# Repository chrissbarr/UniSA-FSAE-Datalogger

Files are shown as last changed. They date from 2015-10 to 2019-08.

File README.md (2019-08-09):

# UniSA FSAE Datalogger
This is an Arduino shield designed to be used for logging data on the UniSA SAE Team's vehicle. It provides interfaces to various components - primarily sensors, but there are also user-interface elements as well.

## Image
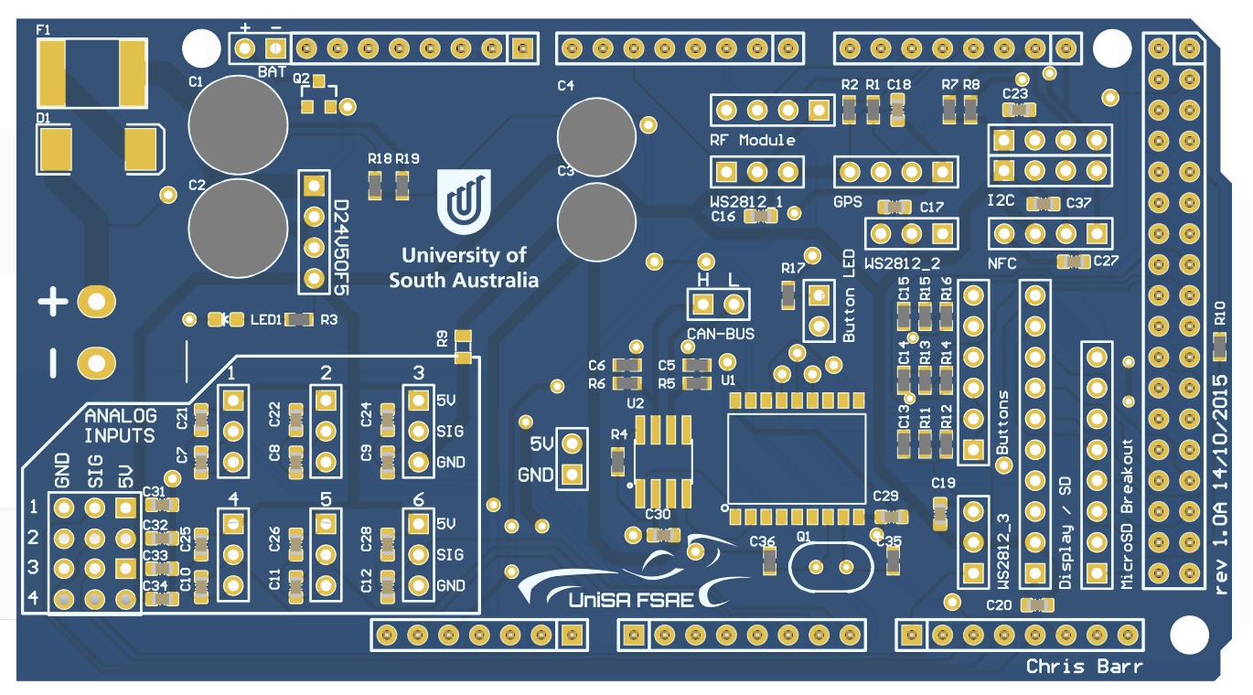
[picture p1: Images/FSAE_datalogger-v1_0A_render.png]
FSAE Datalogger PCB Preview


## Connections
### Sensor Inputs
* GPS
* IR Thermopile
* Thermistors
* Potentiometers
* CAN Bus

### User Interface
* Adafruit OLED Display
* Physical Push-buttons
* NFC Tag Read / Write

### Outputs
* Log Data to microSD Card
* Transmit Data via Wireless Link (UART-based)
* Power and Control WS2812 LEDs for Indication and Illumination

### Power
* Board space / pin header to connect a [Pololu D24V50F5](https://www.pololu.com/product/2851) step-down voltage regulator.
 * 7-38V Input
 * Max. 5A Current
* SMD fuse for short-circuit protection
* Diode for reverse-polarity protection

## Compatibility
Originally designed to be compatible with the Arduino Due, problems with I2C communication between some of the peripherals (primarily the NFC module) and the Due caused a shift to the Arduino Mega2560. Form factor remains unchanged, and the Due may still be useable provided the compatibility issue is overcome or disregarded.

The primary concern is sufficient IO, which the Arduino Uno (and other similar form-factor boards) were lacking. Use of the Arduino Due would allow for the CAN Bus controller inside the AT91SAM3X8E to be used (removing the need for the MCP2515 CAN Bus controller IC).

## Design Images
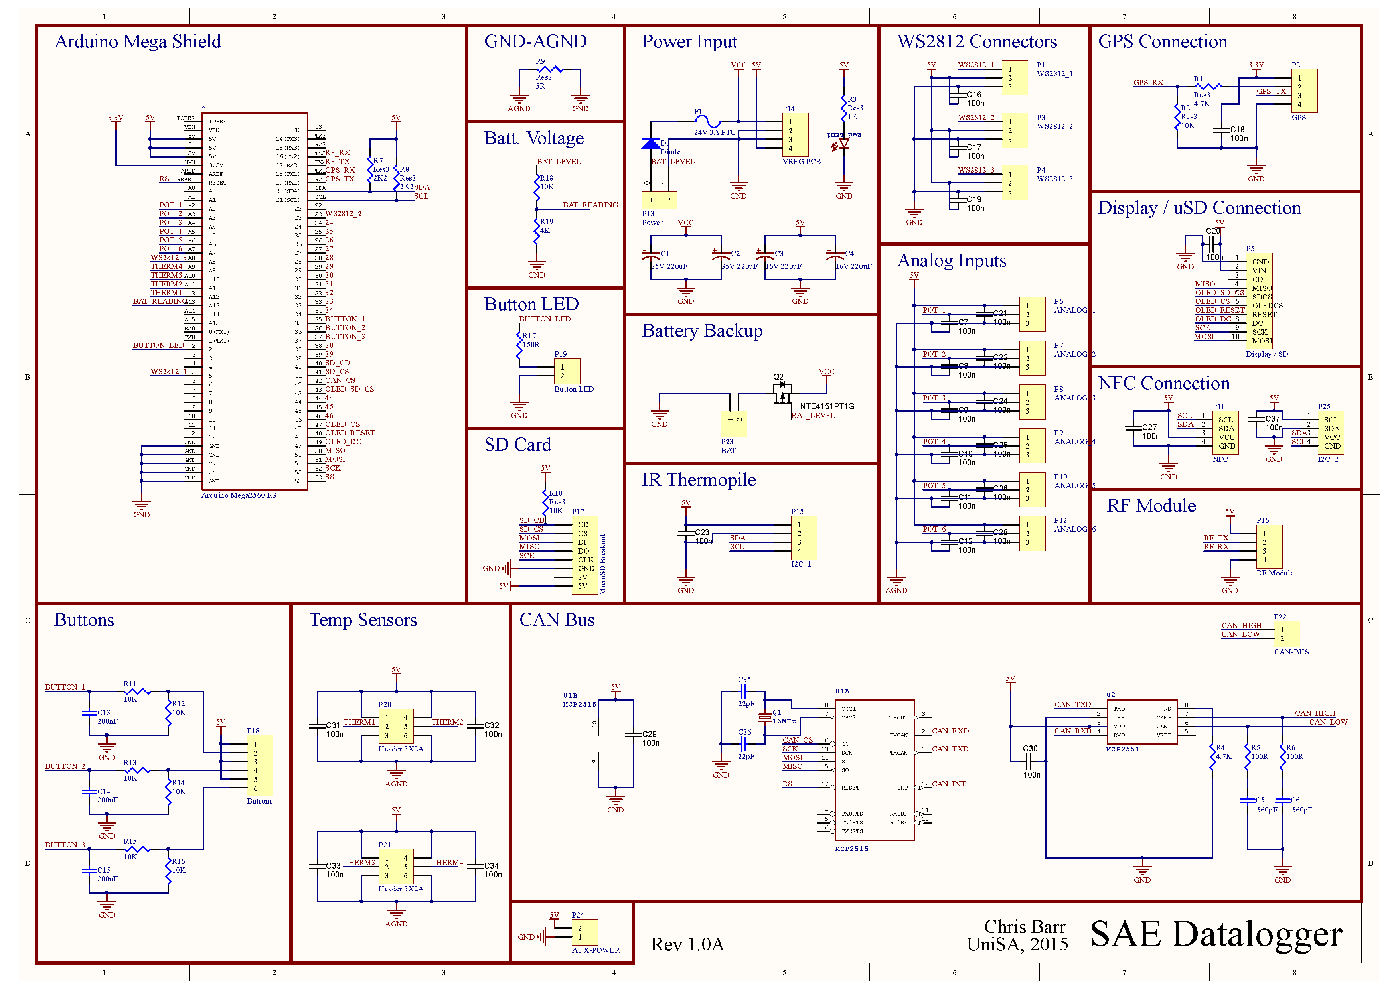
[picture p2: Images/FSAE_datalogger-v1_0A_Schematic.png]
FSAE Datalogger Schematic


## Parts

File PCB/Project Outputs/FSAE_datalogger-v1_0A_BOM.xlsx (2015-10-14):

Designator | Manufacturer | Manufacturer Part Number | Digikey | Comment | Description | Footprint | LibRef | Quantity
C1, C2 | Panasonic Electronic Components | ECA-1VM221 | P5166-ND | 35V 220uF | Electrolytic Capacitor | 8-DIA-CAP-3.5MM-LEADS | Capacitor 50V 470uF | 2
C35, C36 | TDK Corporation | C1608C0G1H220J080AA | 445-1273-1-ND | 22pF | Ceramic Capacitor | 0603 | Cap Semi | 2
C5, C6 | TDK Corporation | C1608C0G1H561J080AA | 445-1290-1-ND | 560pF | Ceramic Capacitor | 0603 | Cap | 2
C13, C14, C15 | TDK Corporation | C1608X7R1C224K080AC | 445-1318-1-ND | 220nF | Ceramic Capacitor | 0603 | Cap | 3
C3, C4 | Panasonic Electronic Components | ECA-1CHG221 | P5530-ND | 16V 220uF | Electrolytic Capacitor | 6.3-DIA-CAP | Capacitor 50V 470uF | 2
C7, C8, C9, C10, C11, C12, C16, C17, C18, C19, C20, C21, C22, C23, C24, C25, C26, C27, C28, C29, C30, C31, C32, C33, C34 | TDK Corporation | C1608X7R1H104K080AA | 445-1314-1-ND | 100nF | Ceramic Capacitor | CAPC1608X90N | CAPC_100n_0603_X7R_50V_10% | 25
D1 | Diodes Incorporated | S5BC-13-F | S5BC-FDICT-ND | Diode | Default Diode | SMC | Diode | 1
F1 | Bourns Inc. | MF-LSMF300/24X-2CT-ND | MF-LSMF300/24X-2CT-ND | 24V 3A PTC | Fuse | MF-LSMF SMD PTC Fuse | Fuse 2 | 1
LED1 | Kingbright | APT1608SURCK | 754-1123-1-ND | Red | Power Indicator | LED-0603 | LED0603 | 1
P1, P3, P4, P6, P7, P8, P9, P10, P12 |  |  |  | WS2812_1 | Header, 3-Pin | HDR1X3 | Header 3 | 9
P2, P11, P14, P15, P16 |  |  |  | GPS | Header, 4-Pin | HDR1X4 | Header 4 | 5
P5 |  |  |  | Display / SD | Header, 10-Pin | HDR1X10 | Header 10 | 1
P13 | On Shore Technology Inc. | OSTTC022162 | ED2609-ND | Power | Screw Terminal, 2-Pin | 2P 5.08mm Screw Terminal | 2P Screw Terminal 5.08mm | 1
P17 |  |  |  | MicroSD Breakout | Header, 8-Pin | HDR1X8 | Header 8 | 1
P18 |  |  |  | Buttons | Header, 6-Pin | HDR1X6 | Header 6 | 1
P19, P22, P23, P24 |  |  |  | Button LED | Header, 2-Pin | HDR1X2 | Header 2 | 4
P20, P21 |  |  |  | Header 3X2A | Header, 3-Pin, Dual row | HDR2X3_CEN | Header 3X2A | 2
Q1 | ECS Inc. | ECS-160-20-46X | XC1759-ND | 16MHz | CrystalsVarious standard crystals. Proven footprints. Spark Fun Electronics SKU : COM-00534 | CRYSTAL-SMD-5X3 | CRYSTAL5X3 | 1
Q2 | ON Semiconductor | NTE4151PT1G | NTE4151PT1GOSCT-ND | P-Channel | MOSFET SMD P-CH 20V 0.76A 0.313W SOT523F | SOT23-3 | MOSFET_P-CH_NTE4151PT1G | 1
R1, R4 | Yageo | RC0603JR-074K7L | 311-4.7KGRCT-ND | 4.7K | Resistor | 0603 | Res3 | 2
R7, R8 | Yageo | RC0603FR-072K2L | 311-2.20KHRCT-ND | 2K2 | Resistor | 0603 | Res3 | 6
R3 | Yageo | RC0603JR-071KL | 311-1.0KGRCT-ND | 1K | Resistor | 0603 | Res3 | 1
R5, R6 | Yageo | RC0603JR-07100RL | 311-100GRCT-ND | 100R | Resistor | 0603 | Res3 | 2
R9 | Yageo | RC0603JR-071RL | 311-1.0GRCT-ND | 1R | Resistor | 0805 | Res3 | 1
R2, R10, R11, R12, R13, R14, R15, R16, R18 | Yageo | RC0603JR-0710KL | 311-10KGRCT-ND | 10K | Resistor | 0603 | Res3 | 6
R17 | Yageo | RC0603JR-07150RL | 311-150GRCT-ND | 150R | Resistor | 0603 | Res3 | 1
R19 | Yageo | RC0603FR-074K02L | 311-4.02KHRCT-ND | 4K | Resistor | 0603 | Res3 | 2
U1 | Microchip Technology | MCP2515T-I/SO | MCP2515T-I/SOCT-ND | MCP2515 | CAN Controller | SO-18W | MCP2510SO | 1
U2 | Microchip Technology | MCP2551-I/SN | MCP2551-I/SN-ND | MCP2551 | CAN Transciever | SO08 | MCP2551 | 1

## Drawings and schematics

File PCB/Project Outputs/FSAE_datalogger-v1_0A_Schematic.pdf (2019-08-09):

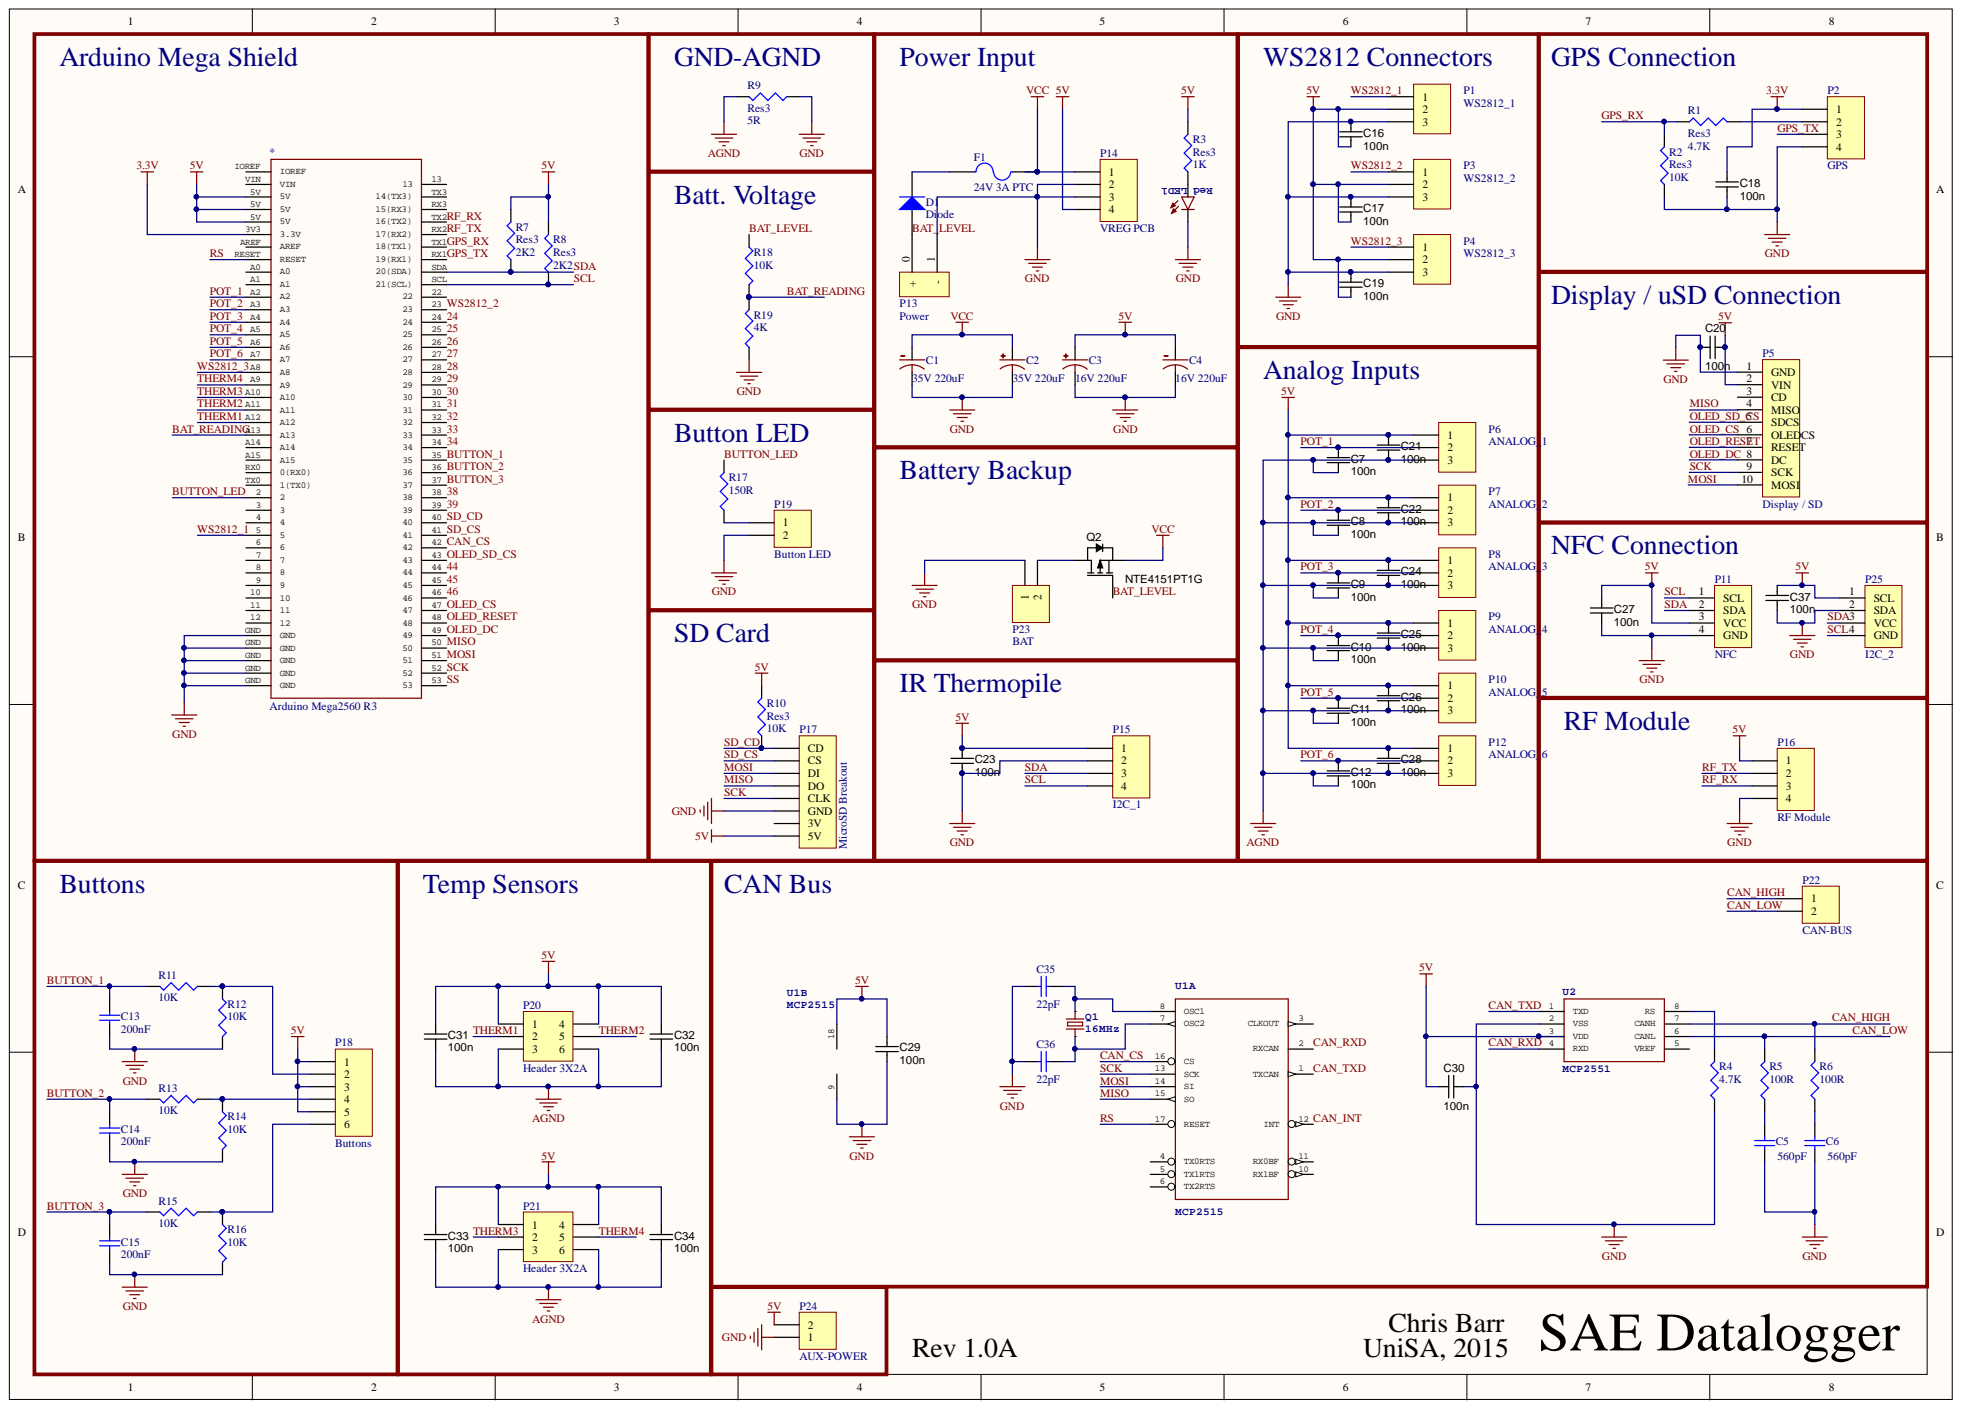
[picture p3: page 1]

5V 5V

GND

SAE Datalogger Chris Barr

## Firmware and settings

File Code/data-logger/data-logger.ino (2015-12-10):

/**************************************************************************/
/*! 
    Datalogger sketch for the UniSA FSAE team.
    
*/
/**************************************************************************/

#define _CAT(a, ...) a ## __VA_ARGS__
#define SWITCH_ENABLED_0 0
#define SWITCH_ENABLED_1 1
#define SWITCH_ENABLED_  1
#define ENABLED(b) _CAT(SWITCH_ENABLED_, b)

#define NFC
#define GPS
#define DISPLAY
#define SDCARD 1  //1 for SD card in display, 2 for SD card in separate breakout
#define BUTTONS
#define EEPROM_ENABLED
#define ANALOG_INPUTS
#define CANBUS


#include <stdio.h>

//NFC Setup
#if ENABLED(NFC)
  //#include <Wire.h>
  #include <PN532_I2C.h>
  #include <PN532.h>
  //#include <NfcAdapter.h>

  PN532_I2C pn532i2c(Wire);
  PN532 nfc(pn532i2c);
#endif

//GPS SETUP
#if ENABLED(GPS)
  #include <TinyGPS++.h>
  
  static const uint32_t GPSBaud = 9600;
  TinyGPSPlus gps;  // The TinyGPS++ object
  
#endif

//Display SETUP
#if ENABLED(DISPLAY)
  #include <Adafruit_GFX.h>
  #include <Adafruit_SSD1351.h>
  #include <SD.h>
  #include <SPI.h>
  
  //#define VERBOSE_DISPLAY
  #define SPLASH_SCREEN_ENABLED
  #define SPLASH_IMAGE "splash.bmp" //file to load from SD card. 
  #define SPLASH_DURATION 1000 //display duration in milliseconds
  
  //OLED Setup
  // You can use any (4 or) 5 pins 
  #define sclk 2
  #define mosi 3
  #define dc   49
  #define cs   47
  #define rst  48
  
  // Color definitions
  #define	BLACK           0x0000
  #define	BLUE            0x001F
  #define	RED             0xF800
  #define	GREEN           0x07E0
  #define CYAN            0x07FF
  #define MAGENTA         0xF81F
  #define YELLOW          0xFFE0  
  #define WHITE           0xFFFF
    
  // use the hardware SPI pins 
  Adafruit_SSD1351 tft = Adafruit_SSD1351(cs, dc, rst);
  
  String output;
  char char_buff[20];

#endif

//SD SETUP
#if ENABLED(SDCARD)
    #define SD_CS 43    

    // the file itself
    File bmpFile;
    
    // information we extract about the bitmap file
    int bmpWidth, bmpHeight;
    uint8_t bmpDepth, bmpImageoffset;

    const int LIMIT = 1000;
    char fileName[13];
    File dataFile;
#endif

//Button SETUP
#if ENABLED(BUTTONS)
  #include <Button.h>        //https://github.com/JChristensen/Button
  #define BUTTON_UP 36
  #define BUTTON_SEL 35
  #define BUTTON_SET 37

  #define PULLUP false
  #define INVERT false
  #define DEBOUNCE_MS 20
  #define LONG_PRESS 1000

  Button button_up(BUTTON_UP, PULLUP, INVERT, DEBOUNCE_MS);    //Declare the button
  Button button_sel(BUTTON_SEL, PULLUP, INVERT, DEBOUNCE_MS);    //Declare the button
  Button button_set(BUTTON_SET, PULLUP, INVERT, DEBOUNCE_MS);    //Declare the button

#endif

#if ENABLED(EEPROM_ENABLED)
  #include <EEPROM.h>

  int eeprom_address = 0;
  int eeprom_options_start_addr = 0;
#endif

#if ENABLED(ANALOG_INPUTS) 
  #define ANALOG1 A2
  #define ANALOG2 A3
  #define ANALOG3 A4
  #define ANALOG4 A5
  #define ANALOG5 A6
  #define ANALOG6 A7

  #define SAMPLE_FREQ 4 //every x'th loop sample and store values

  int analog1, analog2, analog3, analog4, analog5, analog6;
#endif

#if ENABLED(CANBUS) 
  #include <Canbus.h>

  int data;
  char buffer[456];  //Data will be temporarily stored to this buffer before being written to the file
#endif

//timekeeping
#define LOOP_DELAY 20000 // Loop delay in us. This is the desired time between drive calls. Stability ensures accurate velocity calculations and motor control.

// Can put variables for checking accurate loop timing here, eg interupt time and scale factor.
int loop_number = 0; // variable to hold the loop number. Used to keep track of which topics to publish and when
unsigned long loop_time = micros(); // Loop time place holder for motor velocity calculation.
unsigned long last_loop_micros = micros();

int loop_index = 0;

//menu structure
#define MENU_OPTIONS 6
#define MENU_OPTION_HEIGHT 10
int menu_selected_index = 0;
bool menu_changed = false;
bool menu_changed_small = false;
bool menu_active = false;
bool menu_just_opened = false;

enum menu_items {
  GPS_ONOFF,
  LED_BRIGHTNESS,
  SD_LOGGING,
  INVERT_DISPLAY,
  CLEAR_EEPROM,
  NEW_LOGFILE
};

typedef struct menuOption {
  String optionName;
  int numStates;
  int curState;
  String stateText[5];
};

struct menuOption menuArray[MENU_OPTIONS];


//variables to format and display to driver

enum display_variables {
  V_SPEED,
  V_SPEED_AVG,
  V_RPM,
  V_VOLTS,
  V_TEMP,
  V_AMPS,
  V_POWER
};

enum variable_types {
  INT,
  FLOAT,
  BOOL,
  STRING
};

#define NUM_VARIABLES 4

typedef struct displayVariable {
  int type;
  int intVal;
  float floatVal;
  bool boolVal;
  String stringVal;
  String displaySymbol;
  String displayPrefix;
  String displaySuffix;
  int decPoints;
  bool valChanged;
  int symOffset;
};

struct displayVariable displayVariables[NUM_VARIABLES];

long randNumber;
int activeVariableBig = 0;
int activeVariableSmall1 = 0;
int activeVariableSmall2 = 0;
bool indicatorsJustChanged = false;

#define BATT_PIN A13
#define BATT_R1 10000
#define BATT_R2 4000

void setup(void) {
  Serial.begin(115200);

  menu_init();
  variables_init();

  pinMode(cs, OUTPUT);
  digitalWrite(cs, HIGH);  

  #if ENABLED(DISPLAY)
    display_init();
  #endif

  #if ENABLED(SDCARD)
    Serial.print("Initializing SD card...");
  
    if (!SD.begin(SD_CS)) {
      Serial.println("failed!");
      return;
    }
    Serial.println("SD OK!");
  
    #if ENABLED(SPLASH_SCREEN_ENABLED)
      bmpDraw(SPLASH_IMAGE, 0, 0);
      delay(SPLASH_DURATION);
      tft.fillScreen(BLACK);
    #endif

    sd_new_logfile();
  
  #endif

  #if ENABLED(DISPLAY)

    if(nfc_init() && gps_init() && eeprom_init()) {
      tft.setTextColor(GREEN);
      tft.println("All systems pass");   
    } else {
      tft.setTextColor(RED);
      tft.setTextSize(3);
      tft.println("Error");   
      tft.setTextSize(1);
      while(1 < 2);
    }
    tft.setTextColor(WHITE); 

    delay(500);

    tft.fillScreen(BLACK);  
    
  #endif

  randomSeed(analogRead(0));
}

void loop(void) {

  loop_timing(); 

  if(loop_index == 0) {
    calculate_voltage();
    loop_index++;
  } else if (loop_index == 1) {
    gps_update();
    loop_index++;
  } else if (loop_index == 2) {
    analog_update();
    loop_index++;
  } else if (loop_index == 3) {
    log_to_sd();
  } else if (loop_index == 4) {
    displayVariables[V_RPM].intVal = canbus_get_rpm();
    loop_index = 0;
  }

  button_update();

  // operate menu / status display
  menu_buttons();   
  if(menu_active) {
    menu_draw();
  } else {
    status_draw();
  }
    
  //nfc_update();
  update_actions();

  // test changing variable (speed)
  randNumber = random(10);

  if(randNumber == 2) {
    displayVariables[V_SPEED].floatVal += (random(-500,500)/1000.0);
    displayVariables[V_SPEED].valChanged = true;
  }

}

void status_draw() {
  
  bool blankScreen = false; //if true, screen will be erased (i.e. when switching from menu to status)
  
  if (button_up.pressedFor(LONG_PRESS) && indicatorsJustChanged == false) {
    Serial.println("Changing big variable...");
    activeVariableBig++;
    indicatorsJustChanged = true;
    blankScreen = true;
  
    if (activeVariableBig >= NUM_VARIABLES)
      activeVariableBig = 0;
  }

  if(menu_changed) {
    blankScreen = true;
    menu_changed = false;
    indicatorsJustChanged = true;
  }

  if(blankScreen) {
    tft.fillScreen(BLACK);  
    print_variable_big(activeVariableBig, 20, 20, 2, WHITE);
  } 
  
  if(indicatorsJustChanged) {
    displayVariables[activeVariableBig].valChanged = true;
  } 
    
  print_variable_big(activeVariableBig, 20, 20, 2, WHITE);

  if(indicatorsJustChanged && button_up.wasReleased())
    indicatorsJustChanged = false; 
}

////////////////////////////////////////////////////////////////////
//                        GENERAL FUNCTIONS                       //
////////////////////////////////////////////////////////////////////

//checks and tracks state of buttons, call frequently
void button_update() {
  button_up.read();
  button_sel.read();
  button_set.read();
}

//maintains consistent loop timing, assuming LOOP_DELAY is large enough
void loop_timing()
{
  while(micros() - last_loop_micros < LOOP_DELAY - 10)
  {
    delayMicroseconds(20); // This loop timing is inaccurate and does not take processing time into account. A better timing function is required.
  }
  //unsigned long temp_last_micros = last_loop_micros;
  last_loop_micros = micros();
  //Serial.println(last_loop_micros-temp_last_micros);
}

//Used to print "GPS...     " etc consistently when initialising
//called by initialisation functions upon startup
void beginTestPrint(char *moduleName) {
  tft.print(moduleName);
  tft.print("...");
  for(int i = 0; i < 14-strlen(moduleName); i++)
    tft.print(" ");
}

//Used to print "pass" or "fail" etc consistently when initialising
//called by initialisation functions after success / failure
void completeTestPrint(bool pass) {
  if(!pass) {
    tft.setTextColor(RED);
    tft.print("FAIL");
  } else {
    tft.setTextColor(GREEN);
    tft.print("pass");
  }
  tft.setTextColor(WHITE);
}

////////////////////////////////////////////////////////////////////
//                             CAN-BUS                            //
////////////////////////////////////////////////////////////////////

bool canbus_init() {
  #if ENABLED(CANBUS) 
    bool success;
    beginTestPrint("CAN-BUS");
    if(Canbus.init(CANSPEED_500))  /* Initialise MCP2515 CAN controller at the specified speed */
      {
        Serial.println("CAN Init ok");
        success = true;
      } else
      {
        Serial.println("Can't init CAN");
        success = false;
      } 
  
      completeTestPrint(success);
      return success;
    #else
      return true;
    #endif
}

int canbus_get_rpm() {
  
  int engine_rpm = 5000;
  
  #if ENABLED(CANBUS) 
    Canbus.ecu_req(ENGINE_RPM, buffer);
    Serial.print("Engine RPM: ");
    Serial.println(buffer);

    engine_rpm = atoi(buffer);
  #endif

  return engine_rpm;    
}

////////////////////////////////////////////////////////////////////
//                           OLED DISPLAY                         //
////////////////////////////////////////////////////////////////////

bool display_init() {
  tft.begin();
  //tft.setRotation(1);
  tft.fillScreen(BLACK);
  //tft.setTextColor(WHITE);
  //tft.print("Display...    ");
  //tft.setTextColor(GREEN);
  //tft.println("pass"); 
  tft.setTextColor(WHITE);
  return true;
}

void displayTest() {
  for(int i = 0; i < 100; i++) {
    displayPrint("Test ",WHITE);
    tft.println(i);
    
    delay(500);
  }
}

//deprecated I think, just use tft.print(etc) - much more flexible and built in.
void displayPrint(char *text, uint16_t color) {
  if(tft.getCursorY()>tft.height()-10) {
    tft.fillScreen(BLACK);
    tft.setCursor(0,0);
  }
  tft.setTextColor(color);
  tft.print(text);
  Serial.print(text);
}

////////////////////////////////////////////////////////////////////
//                   VARIABLE DISPLAY FORMATTING                  //
////////////////////////////////////////////////////////////////////

//configure different variables for display. These variables are also logged automatically.
//To add new variables, add variable ENUM to the ENUM list before setup. Increase variable count define.
//Add variable details below.
void variables_init() {
  displayVariables[V_SPEED].type = FLOAT;
  displayVariables[V_SPEED].floatVal = 75;
  displayVariables[V_SPEED].displaySuffix = "km/h";
  displayVariables[V_SPEED].displaySymbol = "VEL";
  displayVariables[V_SPEED].decPoints = 1;
  displayVariables[V_SPEED].valChanged = true;
  displayVariables[V_SPEED].symOffset = 0;

  displayVariables[V_SPEED_AVG].type = FLOAT;
  displayVariables[V_SPEED_AVG].floatVal = 5;
  displayVariables[V_SPEED_AVG].displaySuffix = "km/h";
  displayVariables[V_SPEED_AVG].displaySymbol = "AVG";
  displayVariables[V_SPEED_AVG].decPoints = 1;
  displayVariables[V_SPEED_AVG].valChanged = true;
  displayVariables[V_SPEED_AVG].symOffset = 20;

  displayVariables[V_RPM].type = INT;
  displayVariables[V_RPM].intVal = 2500;
  displayVariables[V_RPM].displaySymbol = "RPM";
  displayVariables[V_RPM].valChanged = true;
  displayVariables[V_RPM].symOffset = 40;

  displayVariables[V_VOLTS].type = INT;
  displayVariables[V_VOLTS].intVal = 0;
  displayVariables[V_VOLTS].displaySymbol = "BAT";
  displayVariables[V_VOLTS].displaySuffix = "V";
  displayVariables[V_VOLTS].valChanged = true;
  displayVariables[V_VOLTS].symOffset = 60;
}

//prints a given variable at a chosen size, selectable coordinates, colour etc.
// draws the 'symbol' ('VEL', 'REV', 'TEMP' etc above value at location set on variable creation.
// only draws on variable change - to force, set displayVariables[var].valChanged = true;
void print_variable_big(int var, int x, int y, int t_size, uint16_t color) {

  if(displayVariables[var].valChanged == true) {
    
    String variableValue = formatted_variable(var);
  
    int symOffsetX = 0+displayVariables[var].symOffset;
    int symOffsetY = -10;
    int width = (variableValue.length() * (5 * t_size)) - symOffsetX;
    int height = (7 * t_size) - symOffsetY;
  
    tft.fillRect(x+symOffsetX,y+symOffsetY,width,height,BLACK);
  
    tft.setCursor(x,y);
    tft.setTextColor(color);
    tft.setTextSize(t_size);
  
    tft.print(variableValue);
    
    tft.setTextSize(1);
    tft.setCursor(x+symOffsetX,y+symOffsetY);
    
    tft.print(displayVariables[var].displaySymbol);

    displayVariables[var].valChanged = false;
  }
}

//returns a formatted string containing a given variable, 
//including any prefix and suffix (i.e. 'km/h', 'W', 'A', 'V', '/s')
String formatted_variable(int var) {
  String formatted;
  
  formatted = displayVariables[var].displayPrefix;
  
  formatted += string_variable(var);

  formatted += displayVariables[var].displaySuffix;

  return formatted;
}

//I'm retarded, there's a better way to do this I'm sure. Mental block, I swear.
//Variables can be int, float, boolean or string - we want one interface regardless.
//function takes in variable index and returns string containing variable, with no 
//knowledge of variable type required as input.
//These strings are used to build the text displayed to the user, and this value 
//is also directly used when logging to the SD card.
String string_variable(int var) {
  if(displayVariables[var].type == INT)
    return String(displayVariables[var].intVal);
  if(displayVariables[var].type == FLOAT)
    return String(displayVariables[var].floatVal,displayVariables[var].decPoints);
  if(displayVariables[var].type == BOOL)
    return String(displayVariables[var].boolVal);
  else
    return displayVariables[var].stringVal;
}


////////////////////////////////////////////////////////////////////
//                         MISC INPUTS                            //
////////////////////////////////////////////////////////////////////

//reads the analog inputs designed for potentiometers (or similar), spaced separately on the board.
void analog_update() {
  analog1 = analogRead(ANALOG1);
  analog2 = analogRead(ANALOG2);
  analog3 = analogRead(ANALOG3);
  analog4 = analogRead(ANALOG4);
  analog5 = analogRead(ANALOG5);
  analog6 = analogRead(ANALOG6);
}

//reads the analog value and calculates the voltage of the battery / power source.
void calculate_voltage() {
  int Vin = (analogRead(BATT_PIN) * 5)/1024;
  int prevVolts = displayVariables[V_VOLTS].intVal;
  displayVariables[V_VOLTS].intVal = (Vin * (BATT_R1 + BATT_R2)) / BATT_R2;

  if(abs(displayVariables[V_VOLTS].intVal - prevVolts) != 0)
    displayVariables[V_VOLTS].valChanged = true;
}

////////////////////////////////////////////////////////////////////
//                             GPS                                //
////////////////////////////////////////////////////////////////////

bool gps_init() {
  #if ENABLED(GPS)
    beginTestPrint("GPS");
    Serial1.begin(GPSBaud);
    
    unsigned long gps_starttime = millis();
    
    while(millis() - gps_starttime < 2000) {
      while (Serial1.available() > 0)
        gps.encode(Serial1.read());
    }
    
    if(gps.charsProcessed() < 10) {
        completeTestPrint(false);
      return false;
    } else {
        completeTestPrint(true);
      return true;
    }
  #else
    return true;
  #endif
}

void gps_update() {
  #if ENABLED(GPS)
    while (Serial1.available() > 0)
      gps.encode(Serial1.read());
  #endif
}

//old test function, probably not relevant now but maybe useful reference
void gps_print() {
  #if ENABLED(GPS)
    //int16_t oldCursorX = tft.getCursorX;
    //int16_t oldCursorY = tft.getCursorY;
    
    int bar_y = 110;
    
    tft.fillRect(0, bar_y , tft.width(), tft.height()-bar_y, BLACK);
    
    tft.setCursor(0,bar_y);
    
    tft.print(gps.time.hour());
    tft.print(":");
    tft.print(gps.time.minute());
    tft.print(":");
    tft.print(gps.time.second());
    
    //tft.setCursor(oldCursorX,oldCursorY);
  #endif
}

////////////////////////////////////////////////////////////////////
//                             NFC                                //
////////////////////////////////////////////////////////////////////

bool nfc_init() {
  #if ENABLED(NFC)
    beginTestPrint("NFC");
    nfc.begin();
     
    uint32_t versiondata = nfc.getFirmwareVersion();
    if (! versiondata) {
      completeTestPrint(false); 
      return false;
    }
    
    // Got ok data, print it out!
    completeTestPrint(true); 
    
    #ifdef VERBOSE_DISPLAY
    
    tft.print("Found chip PN5"); tft.println((versiondata>>24) & 0xFF, HEX); 
    tft.print("Firmware ver. "); tft.print((versiondata>>16) & 0xFF, DEC); 
    tft.print('.'); tft.println((versiondata>>8) & 0xFF, DEC);
    
    #endif
    
    // Set the max number of retry attempts to read from a card
    // This prevents us from waiting forever for a card, which is
    // the default behaviour of the PN532.
    nfc.setPassiveActivationRetries(0xFF);
    
    // configure board to read RFID tags
    nfc.SAMConfig();
  #endif
  
  return true;
}

//checks for and reads NFC tag. Very slow, must be used sparingly.
void nfc_update() {
  #if ENABLED(NFC)
    
    boolean success;
    uint8_t uid[] = { 0, 0, 0, 0, 0, 0, 0 };  // Buffer to store the returned UID
    uint8_t uidLength;                        // Length of the UID (4 or 7 bytes depending on ISO14443A card type)
    
    // Wait for an ISO14443A type cards (Mifare, etc.).  When one is found
    // 'uid' will be populated with the UID, and uidLength will indicate
    // if the uid is 4 bytes (Mifare Classic) or 7 bytes (Mifare Ultralight)
    success = nfc.readPassiveTargetID(PN532_MIFARE_ISO14443A, &uid[0], &uidLength);
    
    if (success) {
      tft.println("Found a card!");
      tft.print("UID Length: ");
      
      tft.print(uidLength, DEC);
      tft.print(" bytes");
  
      tft.print("UID Value: ");
      for (uint8_t i=0; i < uidLength; i++) 
      {
        tft.print(" 0x");
        tft.print(uid[i], HEX);
      }
      tft.println("");
      // Wait 1 second before continuing
      delay(1000);
    }
    else
    {
      // PN532 probably timed out waiting for a card
      //displayPrintln("Timed out waiting for a card", WHITE);
    }

  #endif
  
}

////////////////////////////////////////////////////////////////////
//                           EEPROM                               //
////////////////////////////////////////////////////////////////////

void clear_eeprom() {
  for (int i = 0 ; i < EEPROM.length() ; i++) {
    EEPROM.write(i, 0);
  }
  Serial.println("EEPROM Cleared!");
}

bool eeprom_init() {
  #if ENABLED(EEPROM_ENABLED)
    beginTestPrint("EEPROM");

    int eeAddress = eeprom_options_start_addr;
    int tempVar;
    Serial.println("Initialising EEPROM...");

    for(int i = 0; i < MENU_OPTIONS; i++) {
      EEPROM.get(eeAddress + i, tempVar);

      Serial.print(menuArray[i].optionName);
      Serial.print(": ");

      if (tempVar >= 0 && tempVar < menuArray[i].numStates) {
        menuArray[i].curState = tempVar;
        Serial.println(menuArray[i].stateText[tempVar]);  
      } else {
        Serial.println("Error - invalid value!");
      }
      
      delay(200);
    }
  
    completeTestPrint(true);
  #endif
  return true;  
}

////////////////////////////////////////////////////////////////////
//                         MENU SCREEN                            //
////////////////////////////////////////////////////////////////////
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

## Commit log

2015-10-14 Rev 1.0A
    Version at time of first purchase order / PCB fab.
    [SAE_shield.PrjPcb, datalogger.SchDoc, datalogger1.PcbDoc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]
2015-12-08 Arduino Sketch
    Working menu system with button inputs, logging data to SD card.
    [SAE_shield.PrjPcb, datalogger.SchDoc, datalogger1.PcbDoc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]
2015-12-08 Bug fix
    Fix problem where variables may not draw after return from menu screen. Usually variables are only drawn when they change - need to force change after closing menu screen.
    [data-logger.ino]
2015-12-08 Tidying
    Commenting major functions, sorting functions by category / functionality etc. General tidying so Scott doesn't die.
    [data-logger.ino]
2015-12-10 CAN-Bus
    Added basic implementation to fetch ECU RPM and update relevant display variable with value. Untested.
2018-07-27 Tidy PCB files
    Tidy schematic for presentation in report
    Add pinout to PCB for future reference
    [datalogger.SchDoc, datalogger2.PcbDoc]
2019-08-04 Tidy Files
    [FSAE_datalogger-v1_0A_BOM.xlsx, FSAE_datalogger.PcbDoc, FSAE_datalogger.PrjPcb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]
2019-08-09 Add images
    Change PDF to be coloured, add PNG copy + render of board.
2019-08-09 Update README.md
    Add image + schematic to readme
